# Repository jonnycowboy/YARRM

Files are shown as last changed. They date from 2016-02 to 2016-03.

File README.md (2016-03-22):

# YARRM
Yet Another Robot aRM - a human-safe, open HW robotic arm with 7 DOF. Laser-cut steel and 3D Printed Part (eventually molded) construction.
Updated pictures and blog here: https://hackaday.io/project/2055-yarrm-7-dof-low-cost-robot-arm

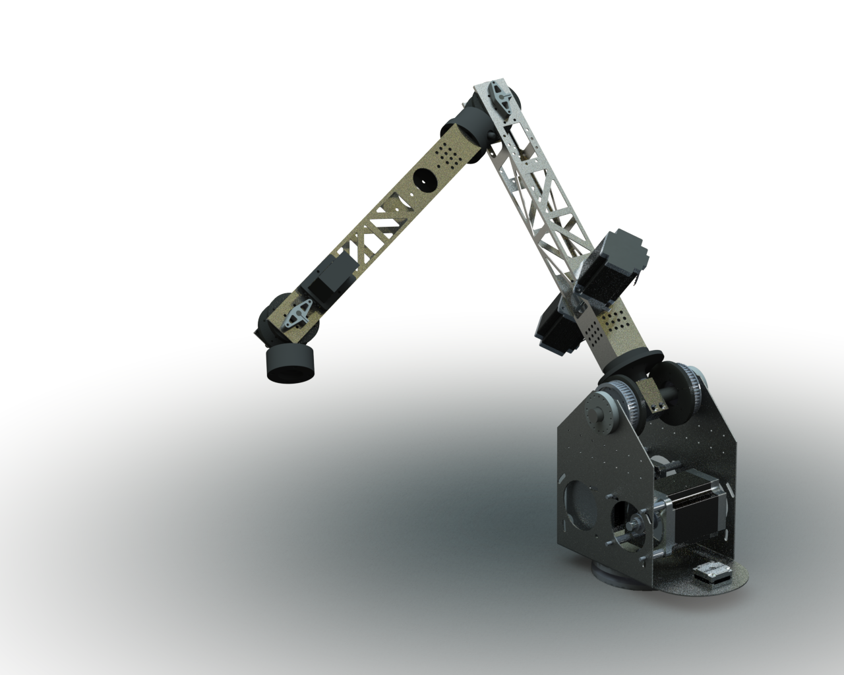
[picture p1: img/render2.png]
assembly render


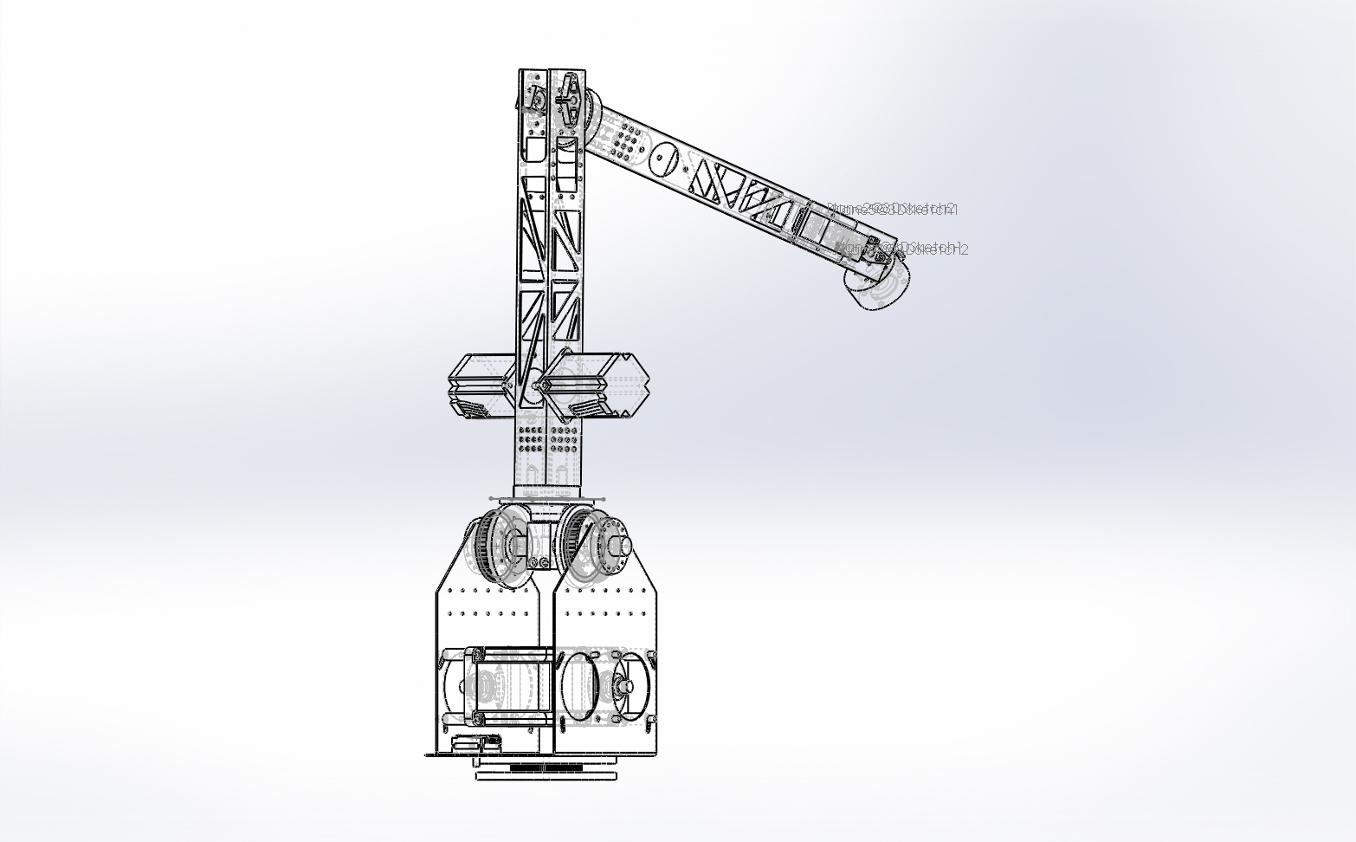
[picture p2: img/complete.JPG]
line drawing


Control will be via visual servoing which sends g-code to a stepper controller.  Similar to what is written here:
http://edinburghhacklab.com/2013/05/robotics-adaptive-control-and-vision/

License: CC-BY-SA (V4.0)

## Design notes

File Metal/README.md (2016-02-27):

## This is the folder where the files (DXF, DWG or SLDPRT) for the metal parts are kept.  

The base has a 16-gauge (~1.6mm) laser-cut steel folded metal base - *ILL_ADBASE_1734.DWG*.  If you get these parts cut yourself, you need to fold them once they are cut, right on the two intersections of the _T_ shape.

The arms are laser-cut 2"x2" square 16ga (~1.6mm) laser-cut steel tubes - *ILL_ADARM_23_400.SLDPRT*.  I will upload another shorter version of this arm in case you might need a different arm configuration. The tubes are in SLDPRT format as that is what my laser cutting supplier uses for tube cuts.

Note: the parts *20mm block.STL* and *8mm block.STL* in the STL folder will likely be moved here as they will be machined out of aluminium to properly preload the bearings and support the cantilever loads.

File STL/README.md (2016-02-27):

## This is the folder where the generated STLs will be kept.  
Github allows for version control so better to have it here than Thingiverse!

Parts should be rotated for best printing orientation.

Note: the parts *20mm block.STL* and *8mm block.STL* are listed here as 3D printed but likely will not survive the first power-on tests of the arm.  They will probably require being cut out of aluminium blocks.  This should not be too difficult, as long as you have access to a drill press it will be feasible.

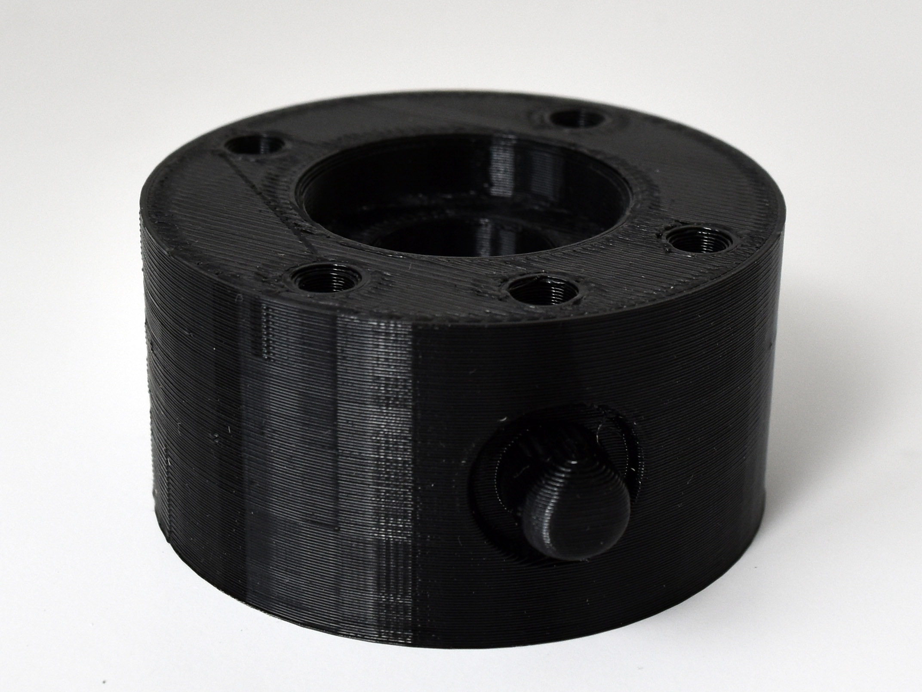
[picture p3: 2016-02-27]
img/ILL_WRIST_UR.JPG

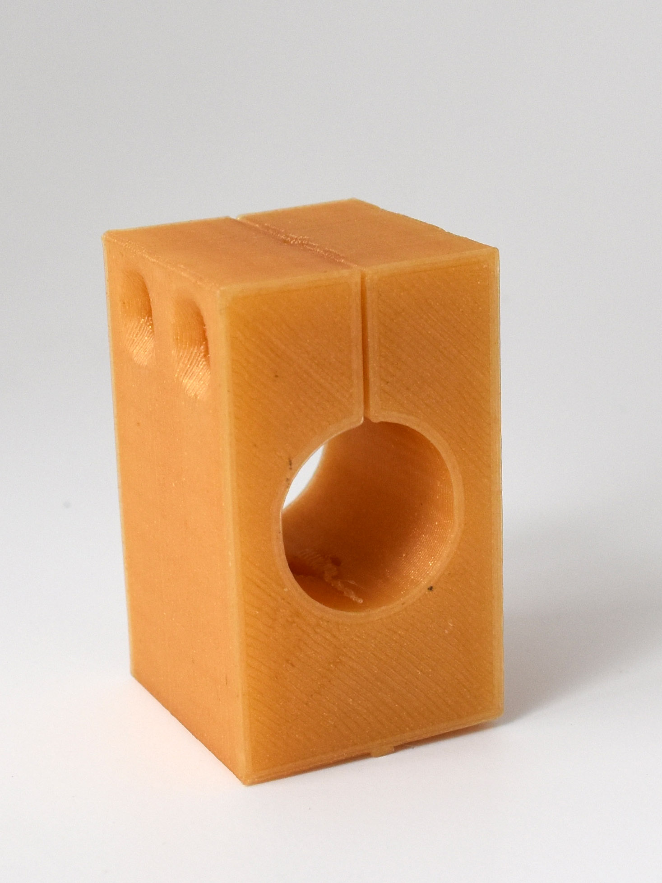
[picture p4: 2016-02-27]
img/ILL_ADBASE_block20.JPG

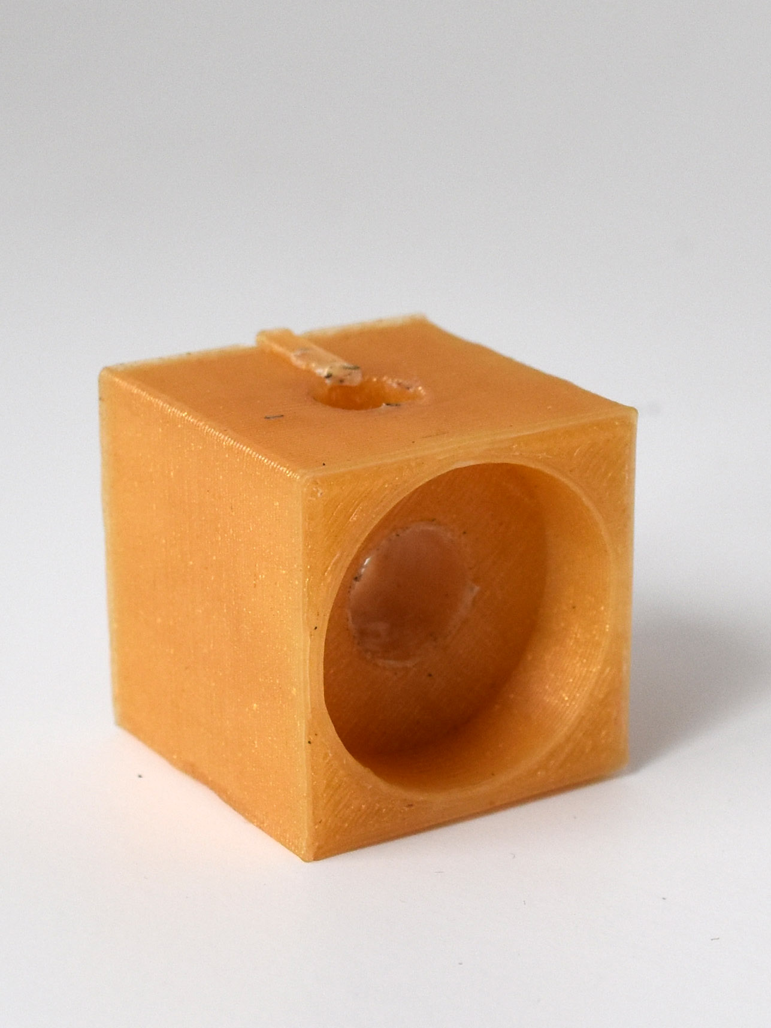
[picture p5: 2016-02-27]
img/ILL_ADARM_block08.JPG

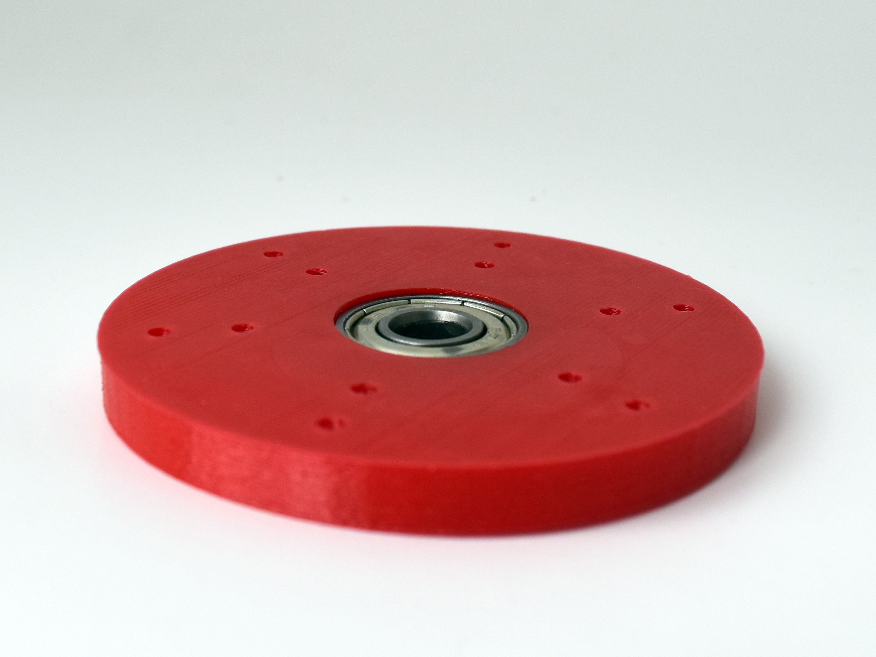
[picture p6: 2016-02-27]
img/ILL_ADARM_flexdisc.JPG

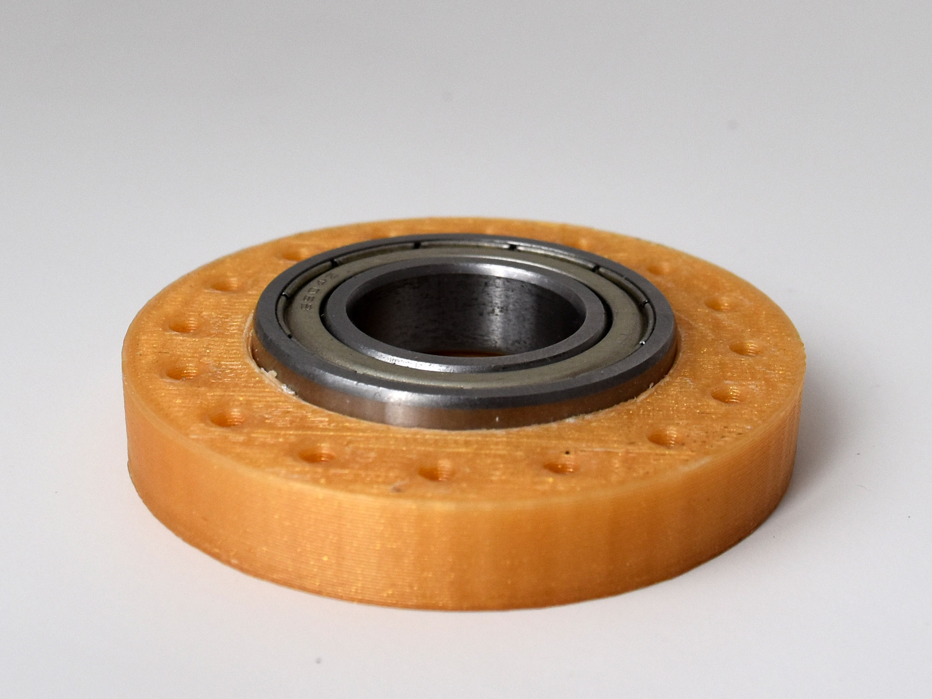
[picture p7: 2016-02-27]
img/ILL_ADBASE_shaftbear20.JPG

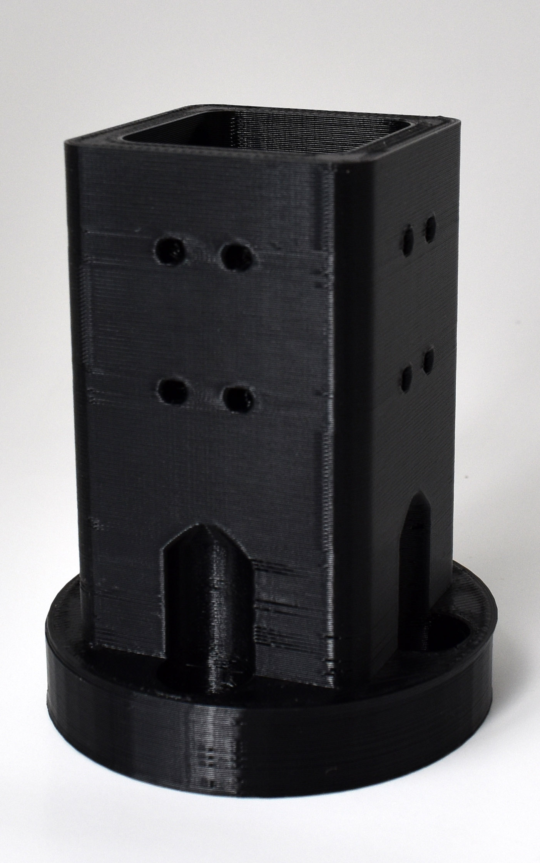
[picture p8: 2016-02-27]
img/ILL_ADARM_mateUR.JPG

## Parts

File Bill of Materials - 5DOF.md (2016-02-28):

# Bill of Materials
### Steel Parts

Component Refs   | Type                  | Details                                    | Qty | Source Link
--------------   | ---------------       | ----------                                 | :-: | ------------
ILL_ADBASE_1734  | 16ga steel plate      | Base with NEMA34 drive and NEMA17 rotation |  1  | HTTPS://ILLROBOT.COM/PARTS/ILL_ADBASE_1734
ILL_ADARM_23_400 | 16ga steel 2"x2" tube | 400mm long arm, NEMA23 mount |  2  | HTTPS://ILLROBOT.COM/PARTS/ILL_ADARM_23_400

### 3D Printed Parts

Component Refs         | Type                           |  Qty | Source Link
--------------          | ---------------               |  :-: | ------------
ILL_ADARM_block08       | center block, 8mm shaft       |   1  | HTTPS://ILLROBOT.COM/PARTS/ILL_ADARM_block08
ILL_ADARM_flexdisc      | flex drive disc, 8mm bearing  |   2  | HTTPS://ILLROBOT.COM/PARTS/ILL_ADARM_flexdisc
ILL_ADARM_mateUR        | UR-mount arm mate             |   2  | HTTPS://ILLROBOT.COM/PARTS/ILL_ADARM_mateUR
ILL_ADARM_servocover    | servo retainer cover          |   2  | HTTPS://ILLROBOT.COM/PARTS/ILL_ADARM_servocover
ILL_ADARM_shaftlock08   | shaft support, 8mm            |   2  | HTTPS://ILLROBOT.COM/PARTS/ILL_ADARM_shaftlock08
ILL_ADARM_twistplate    | twist driven plate, arm       |   1  | HTTPS://ILLROBOT.COM/PARTS/ILL_ADARM_twistplate
ILL_ADBASE_block20      | center block, 20mm shaft      |   1  | HTTPS://ILLROBOT.COM/PARTS/ILL_ADBASE_block20
ILL_ADBASE_flexdisc     | flex drive disc, 20mm bearing |   2  | HTTPS://ILLROBOT.COM/PARTS/ILL_ADBASE_flexdisc
ILL_ADBASE_rotation120t | base rotation pulley, 120T    |   1  | HTTPS://ILLROBOT.COM/PARTS/ILL_ADBASE_rotation120t
ILL_ADBASE_shaftbear20  | shaft bearing, 20mm           |   2  | HTTPS://ILLROBOT.COM/PARTS/ILL_ADBASE_shaftbear20
ILL_ADBASE_twistplate   | twist driven plate, base      |   1  | HTTPS://ILLROBOT.COM/PARTS/ILL_ADBASE_twistplate
ILL_WRIST_UR            | UR wrist mount                |   2  | HTTPS://ILLROBOT.COM/PARTS/ILL_WRIST_UR

### Vitamins

Component Refs | Type            | Details       | Qty | Source Link
-------------- | --------------- | ----------    | :-: | ------------
608            | bearing         |  8mmID-22mmOD |  12  | EBAY
6904Z          | bearing         | 20mmID-37mmOD |  6  | EBAY
SHAFT_20_200   | shaft           | 20mmD-200mmL  |  1  | EBAY
SHAFT_08_150   | shaft           |  8mmD-150mmL  |  2  | EBAY
STEP34_TBD_2A  | stepper         | NEMA34        |  2  | EBAY
STEP23_TBD_2A  | stepper         | NEMA23        |  2  | EBAY
STEP17_TBD_2A  | stepper         | NEMA17        |  1  | EBAY

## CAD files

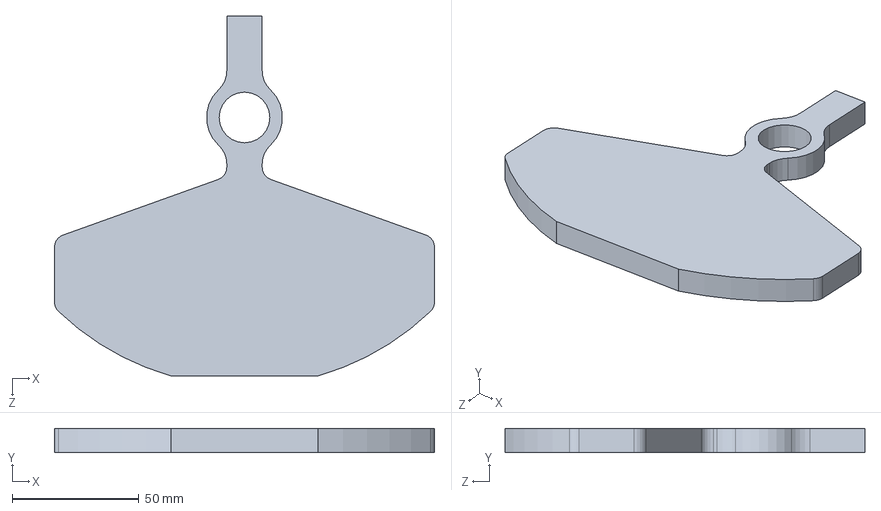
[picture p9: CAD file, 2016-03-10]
Metal/base_counterweight.SLDPRT
150.0 x 9.53 x 142.0 mm

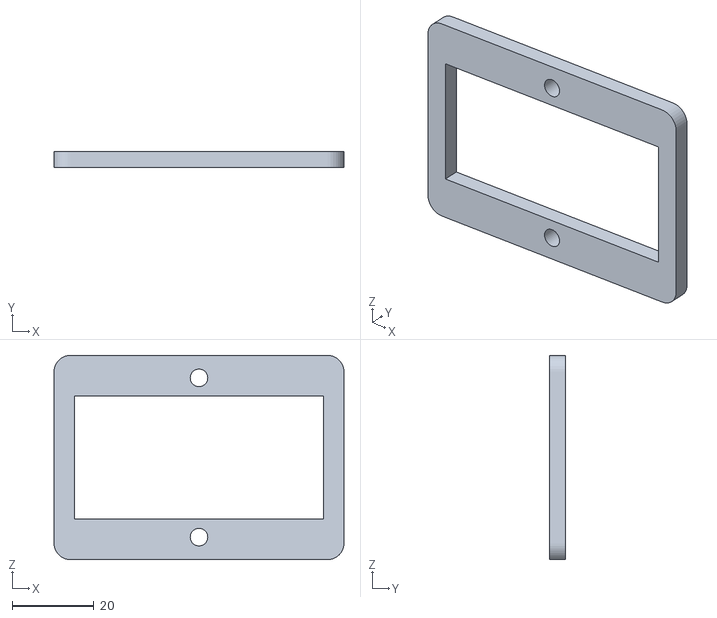
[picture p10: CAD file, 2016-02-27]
STL/servo.cover.STL
71.0 x 4.00 x 50.0

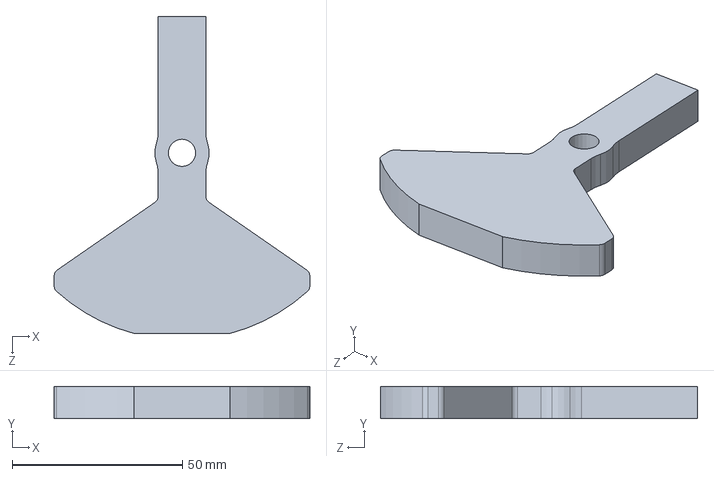
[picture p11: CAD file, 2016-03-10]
Metal/arm_counterweight.SLDPRT
75.0 x 9.53 x 93.0 mm

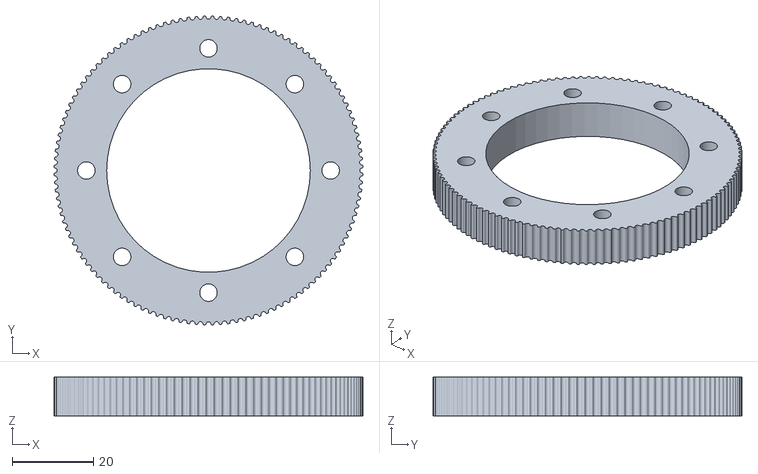
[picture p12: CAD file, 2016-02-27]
STL/120tooth.base.rotation.STL
75.9 x 75.9 x 9.50

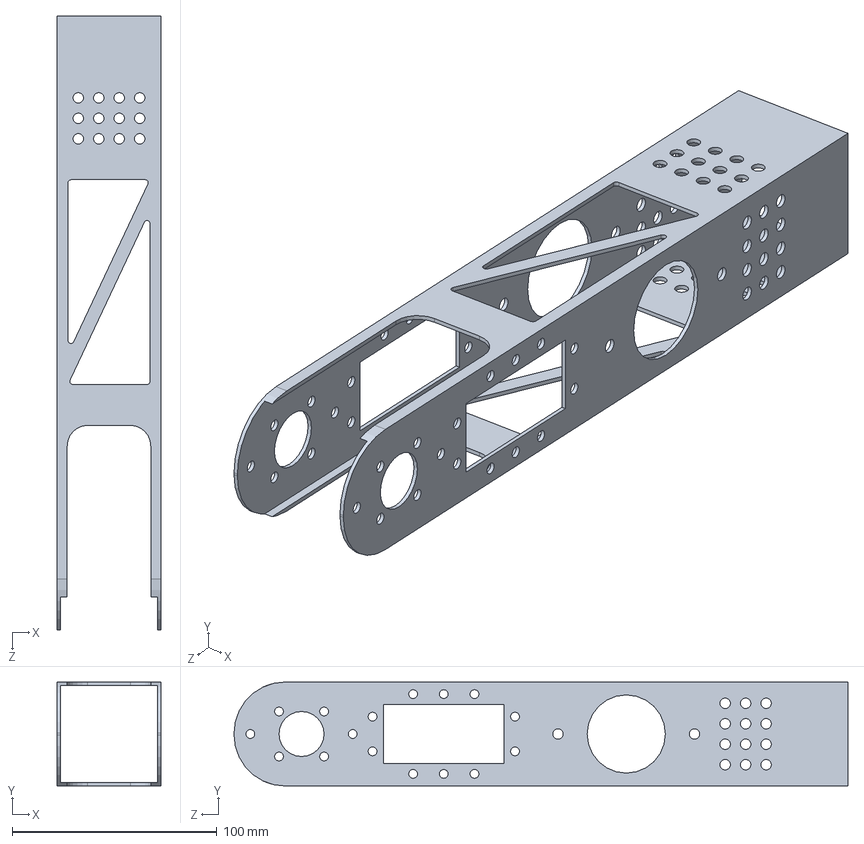
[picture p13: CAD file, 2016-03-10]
Metal/ILL_ADARM_23_250.SLDPRT
50.8 x 50.8 x 300.0 mm

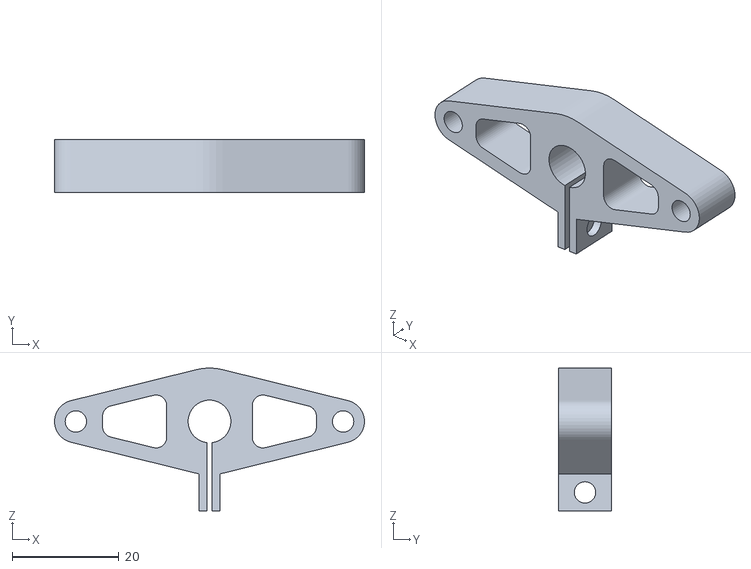
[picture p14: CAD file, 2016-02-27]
STL/lock.block.8mm.STL
58.0 x 10.0 x 26.7

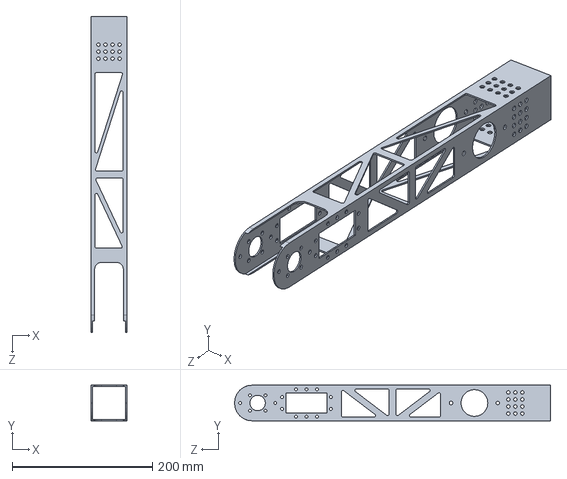
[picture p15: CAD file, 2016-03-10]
Metal/ILL_ADARM_23_400.SLDPRT
50.8 x 50.8 x 450.0 mm

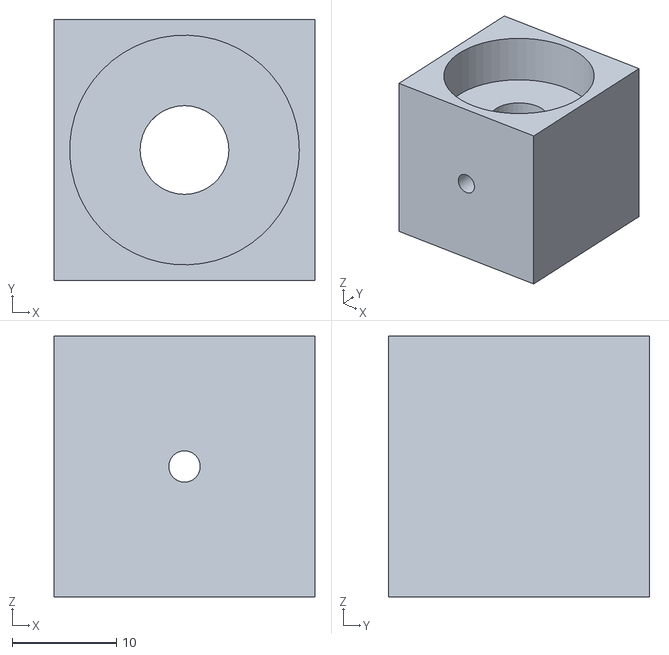
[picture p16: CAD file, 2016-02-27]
STL/8mm.block.STL
25.0 x 25.0 x 25.0

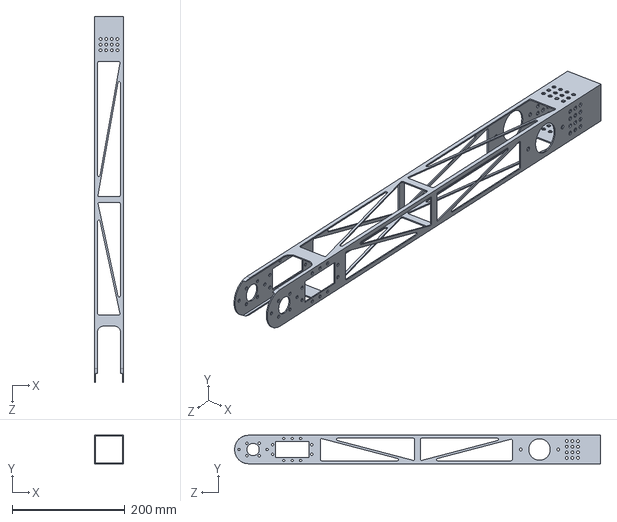
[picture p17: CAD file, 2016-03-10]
Metal/ILL_ADARM_23_600.SLDPRT
50.8 x 50.8 x 650.0 mm

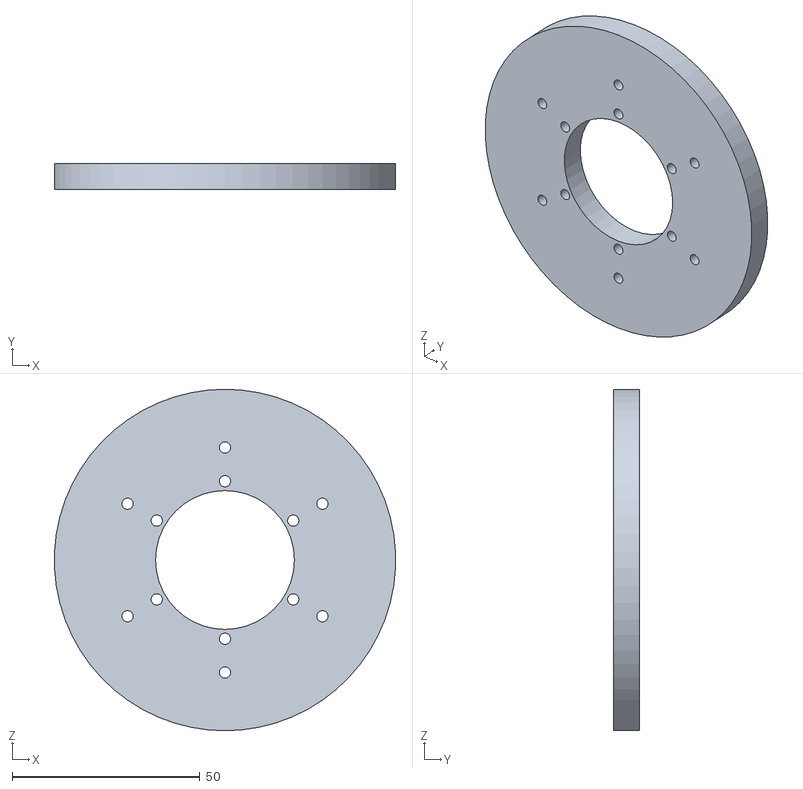
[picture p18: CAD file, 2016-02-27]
STL/base_flexdisc.STL
90.9 x 7.00 x 91.0

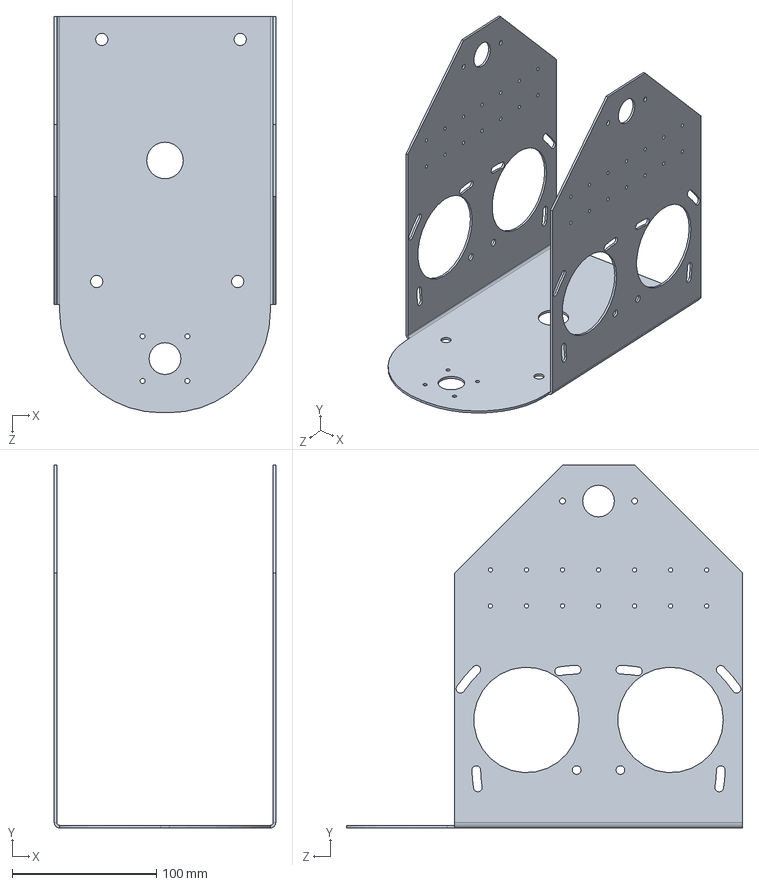
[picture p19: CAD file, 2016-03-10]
Metal/ILL_ADBASE_1734.SLDPRT
153.8 x 251.9 x 275.0 mm

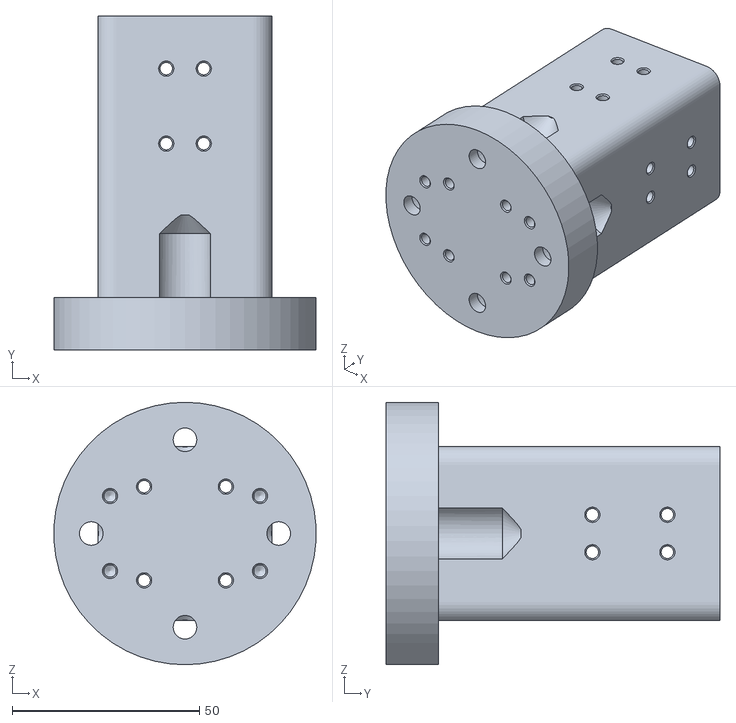
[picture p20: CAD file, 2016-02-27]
STL/ur3.mate.arm.STL
69.9 x 89.0 x 70.0

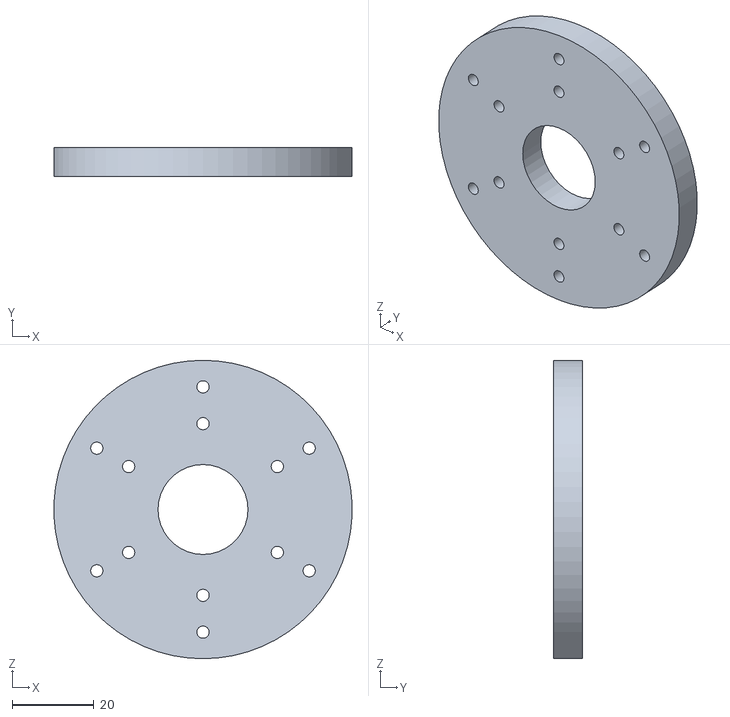
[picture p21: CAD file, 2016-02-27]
STL/arm_flexdisc.STL
72.9 x 7.00 x 73.0

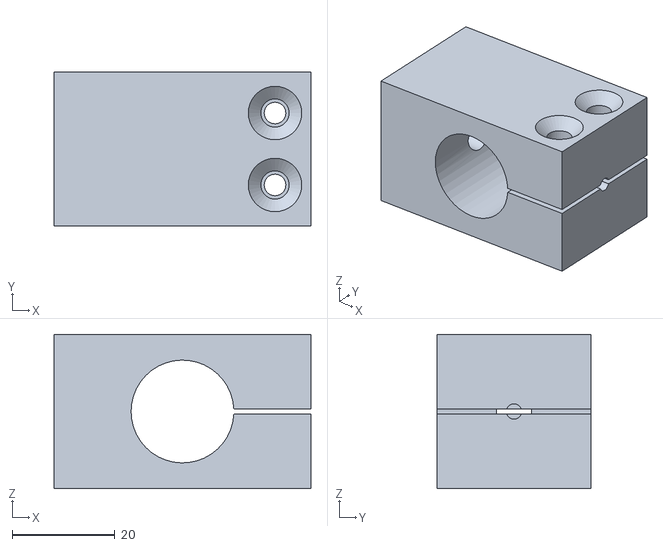
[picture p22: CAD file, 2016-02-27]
STL/20mm.block.STL
50.0 x 30.0 x 30.0

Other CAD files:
STL/20mm.bearing.pocket.STL
STL/UR3.mount.STL
Metal/ILL_ADARM_23_250.STL
Metal/ILL_ADARM_23_400.STL
Metal/ILL_ADARM_23_600.STL
Metal/ILL_ADBASE_1734.DWG
Metal/ILL_ADBASE_1734.STL
Metal/arm_counterweight.STL
Metal/base_counterweight.STL

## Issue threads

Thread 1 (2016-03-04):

Arm tube size is too tight

jonnycowboy, 2016-03-04:
Selecting 2x2" 16ga steel tubing makes it too tight to fit the 2*pulleys, 2*flex-drives and the center pivot block.  Consider changing center block design, or merging pulleys and flex-drives or changing to 2.5"x2.5" tubes.

jonnycowboy, 2016-03-10:
2.5x2.5" tube is not available in 16ga at my laser cutter supplier so I will redesign Interior elements (pulley, flex-disc and pivot blocks) to be narrower.

Closed 2016-03-10.

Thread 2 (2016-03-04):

Redesign pivot blocks on 20mm and 8mm shafts

jonnycowboy, 2016-03-04:
Pivot blocks should be counter-weighted (at least on 20mm shaft) similar to a crankshaft design or spring-loaded to counter-balance the arm weight (static balance) when at full deflection.

jonnycowboy, 2016-03-10:
Closed with [https://github.com/jonnycowboy/YARRM/commit/d0e3cd111887f8dda01929e825d877741c831c3d](https://github.com/jonnycowboy/YARRM/commit/d0e3cd111887f8dda01929e825d877741c831c3d)

Closed 2016-03-10.

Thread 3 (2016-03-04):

Tap hole improvements

jonnycowboy, 2016-03-04:
Some 3D printed blocks have tap drill holes meant to be directly tapped (ie: printed part hole size meets tap drill size), however once printed the holes need to be re-drilled prior to tapping (Too tight). Increase hole size in 3D printed parts.

jonnycowboy, 2016-04-06:
Holes will be re-sized to fit heat-set brass threaded inserts.

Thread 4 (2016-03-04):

Assembly assistance clips

jonnycowboy, 2016-03-04:
3D printed parts should contain latching clips which allow the parts to be set in place in the laser-cut metal for initial assembly without using bolts.

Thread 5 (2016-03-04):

End of metal arm needs to be rounded and shorter

jonnycowboy, 2016-03-04:
With current flex-disc size, it is not possible for the 2nd arm to rotate nor the end effector payload since it hits the corner of the metal arm at around 15-20 degrees deflection.  Flexdisc size could be increased but mainly the corners of the tubes should be rounded.
Note that the redesign of the 8mm shaft clamps (which will change to bearings) will allow to shorten the end.

jonnycowboy, 2016-03-10:
Closed with
[https://github.com/jonnycowboy/YARRM/commit/426fea0cdad5f45643cdb0908491914f6a705027](https://github.com/jonnycowboy/YARRM/commit/426fea0cdad5f45643cdb0908491914f6a705027)

Closed 2016-03-10.

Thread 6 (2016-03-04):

Create shorter arm

jonnycowboy, 2016-03-04:
A shorter version of the 400mm arm should be created with most of the truss-cuts removed in case somebody wants a shorter version.

jonnycowboy, 2016-03-10:
Closed with 426fea0
[https://github.com/jonnycowboy/YARRM/commit/426fea0cdad5f45643cdb0908491914f6a705027](https://github.com/jonnycowboy/YARRM/commit/426fea0cdad5f45643cdb0908491914f6a705027)

Closed 2016-03-10.

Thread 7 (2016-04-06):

Leaf Spring arm counter-balance

jonnycowboy, 2016-04-06:
The arms will need to use a spring to counter-balance any off-center movement.  The best solution is to use the laser-cutting process already in use and directly cut a leaf spring into the arm.

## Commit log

2016-02-16 Create Bill of Materials - 5DOF.md
    Temporary placeholder. Will update with correct quantities and items, then copy to the 7DOF model and fork for the gripper BOM.
2016-02-16 Update Bill of Materials - 5DOF.md
    Removing bad / copied items
2016-02-27 Initial upload of STLs for all of the 3D printed parts
    [120tooth.base.rotation.STL, 20mm.bearing.pocket.STL, 20mm.block.STL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]
2016-02-27 correct naming
    [ILL_ADARM_23_400.SLDPRT, ILL_ADBASE_1734.DWG]
2016-02-28 updated 3D printed parts
2016-03-10 Added 3D base and associate STL files for the metal parts
    [ILL_ADARM_23_400.STL, ILL_ADBASE_1734.SLDPRT, ILL_ADBASE_1734.STL]
2016-03-10 Add multiple arm sizes, round tube ends
    Corrections for issues 5 and 6.
    5] end of arm has been fillet'd to allow arm rotation to clear
    6] a shorter (250mm is shortest) and longer (600mm) long arm were
    created
    [ILL_ADARM_23_250.SLDPRT, ILL_ADARM_23_250.STL, ILL_ADARM_23_400.SLDPRT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]
2016-03-10 Redesigned pivot blocks
    to close items 1 & 2
    1] made pivot narrower to support 2x2" tube
    2] redesigned pivots as counter-weights. Arm counter-weight block will
    probably have to have an additional spring.
    [arm_counterweight.SLDPRT, arm_counterweight.STL, base_counterweight.SLDPRT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]
2016-03-14 added visual servoing link
